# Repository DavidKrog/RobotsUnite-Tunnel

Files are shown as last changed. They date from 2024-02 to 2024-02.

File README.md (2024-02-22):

# RobotsUnite-Tunnel
Autor: <br> 
Celina Engel <br>
David Kroginski

## Hardware (Aufbau der Holzbox):
1.	**Maße der verschiedenen Bauelemente:**

Für den Bau der Holzkiste haben wir mit 10 Bauteile gerechnet, damit die Kiste stabil ist, allen Anforderungen entspricht und die erwünschten Funktionsweisen umgesetzt werden können.

Verwendet haben wir dafür:
   - 4x Seitenwände (50x65cm)
   - 2x für Deckel und Boden (50x50cm)
   - 1x zweiter Boden für den Elektronikabteil (47x47cm)
   - 2x Schiebetüre (37x37cm)
   - 1x Klappe für den Deckel (40x40cm)
<br>
<br>

2. **Maße der Ausschnitte:**

Ausschnitte haben wir an allen Seitenteilen der Holzkiste zur Stabilisierung vorgenommen (siehe Stabilisierung der Box).
   Außerdem haben wir mittig in den Deckel ein 40x40cm großes Quadrat geschnitten, um die Klapptüre für die Technikbox zu realisieren.
   Für die Schiebetüren haben wir ein 35,5x34 cm (Höhe x Breite) großes Rechteck herausgeschnitten.
   Damit die Schiebetüren auf- und zufahren können mussten an der rechten Außenwand Einschnitte vorgenommen werden. Diese wurden passgenau zum Türaufbau gewählt. 
  |  |
:-------------------------:|:-------------------------:|:-----:
<em>Ausschnitte Schiebetüre</em>| <em>Ausschnitt Deckel</em>|<em>Ausschnitte für den Auszug der Schiebetüren</em>

<br>
<br>

**Maßstab:**

Tür_Vorne |  Tür_Hinten|rechte_Seite
:-------------------------:|:-------------------------:|:-----:
<em>Türwand Vorne</em>| <em>Türwand Hinten</em>|<em>Rechte Seite</em>
Boden|Klappe_Deckel|Deckel
<em>Bodenplatte</em>| <em>Deckelplatte</em>|<em>Klappe</em>
zwischenboden|Tür|linke_Seite
<em>Zwischenplatte</em>| <em>Tür</em>|<em>Linke Seite</em>

Bei dem Zwischenboden muss man Aussparungen für Kabel und eventuell für den Endlagentaster machen. Diese sind nicht in der Skizze eingetragen, da dies je nach Montage der Elektrik in Größe und Position variiert.
<br>
<br>

3. **Stabilisierung der Box:**

Um die Holzkiste sehr stabil zu bauen haben wir uns ein simples System überlegt. Hierzu haben wir an jeder Außenkante der einzelnen Holzplatten die Hälfte der Seite um jeweils 1,5cm ausgesägt und die andere Hälfte unberührt gelassen. Somit hat sich ein recht einfaches, aber effizientes Stecksystem ergeben, welches nach der Verschraubung sich als sehr stabil und robust erwiesen hat.

  |  
:-------------------------:|:-------------------------:
<em>Ausschnitte an den Seitenwänden<em>| <em>Ausschnitte an den Seitenwänden</em>

<br>
<br>

4. **Aufteilung der Box in Arena- und Technikabteil:**

Die Holzkiste wird in einen Arena- und Technikabteil aufgeteilt.
Die Arena befindet sich in den unteren zwei Dritteln der Kiste und kann über die beiden verbauten Schiebetüren betreten und genutzt werden. Die Technik im oberen Drittel der Kiste ist einfach über den klappbaren Deckel auf der Oberseite der Box erreichbar. Im inneren der Kiste haben wir einen zweiten Boden verbaut, um die beiden Abteile abzutrennen.
Um den zweiten Boden einzubauen, werden zwei Querstreben in der Kiste verschraubt. Die Position wird von der Schiebetür und den verwendeten Auszugsschienen bestimmt. Auf diesen wird der zweite Boden angebracht.
<p>
    
   <br>
    <em>Balken zur Anbringung der Schiebetüren</em>
</p>

Bis auf die verbauten Motoren für die elektrischen Schiebetüren und die Leuchttaster für das Öffnen und Schließen dieser befinden sich alle elektrischen Bauteile in dem Technikabteil. Diese Aufteilung haben wir vorgenommen, um so gut wie alle Elektrischen Bauteile vom Rest der Box abtrennen zu können, um so mögliche Elektrounfälle zu vermeiden.
<p>
    
    <br>
    <em>Leuchtdrucktaster im Kisteninneren</em>
</p>

<br>
<br>

5. **Schiebetürmechanismus (3D-Druck und Modell der Zahnradschiene und Zahnrad):**

Die verbauten Schiebetüren wurden ein kleines bisschen Größer als der Ausschnitt an der Vorder- und Rückseite gewählt. Damit wollen wir gewährleisten, dass die Türen bündig am Gehäuse anliegen und seitlich nicht durch Schlitze hindurchgeschaut werden kann.  
Außerdem wurde am Boden eine Aussparung eingefräst, in dieser wir eine Führungsschiene verlegt haben. Somit verhindern wir, dass sich die Holztüren verhaken können.  
Damit sich die Türen leicht öffnen und schließen haben wir uns für den Verbau von Schubauszügen entschieden. Diese lassen sich sehr leicht und ohne großen Kraftaufwand bewegen.
Um die Türen elektrisch antreiben zu können wurde eine 37cm lange Zahnradschienen mit dem passenden Zahnrad 3D-Drucker gedruckt. Die Schienen werden mittig an der Schiebetürinnenseite, an den dafür vorgesehenen Laschen befestigt. Das Zahnrad wird passgenau an den Elektromotoren befestigt. Letztendlich wird der Motor in der Kiste so angebracht, dass sich das Zahnrad passend in der Zahnradschiene bewegt um die Schiebetüren auf- und zufahren lassen zu können. 
Damit die Schiebetüre problemlos aufgehen kann haben wir an der rechten Seitenwand passend Ausschnitte vorgenommen (siehe Maße der Ausschnitte). 
  |  |
:-------------------------:|:-------------------------:|:-----:
<em>Schiebetüre vorne<em>| <em>Schiebetüre hinten</em>| <em>Schiebetüre hinten ausgezogen</em>
  |  |Befestigungtür
<em>Boden der Holzkiste<em>| <em>Schiebetüren verbaut</em>| <em> Befestigung der Schiene</em>

<br>
<br>

6.	**Aufbauplan:**

<p>
    
    <br>
    <em>Aubau Holzkiste komplett</em>
</p>

<br>
<br>

7. **Verbesserungen:**
 
Während der Konstruktion haben wir gemerkt, dass nicht alles machbar ist, wie wir es geplant hatten. Dadurch mussten wir manchmal bisschen improvisieren. Dies ist einer der Gründe, warum die rechte Seite der Box die besondere Aussparung für die Schiebetür besitzt.
Damit die äußere Erscheinungsform der Box ordentlicher ist und man aus den Erfahrungen profitieren kann, haben wir für den Aufbau der Kiste teilweise die Maße noch einmal angepasst.

| ||
| --- | --- |
Boden_Verändert| Bodenplatte: <br>Aufgrund der vorher festgelegten Stabilitätsausschnitte würde eine Freifläche vor den Schiebetüren entstehen. Um diese zu vermeiden, wurden die Aussparungen an der Bodenplatte angepasst. Dies soll das Aussägen der einzelnen Teile und das spätere zusammenbauen erleichtern.|
Tür verändert| Schiebetüre: <br>Die Montage der Auszugsschiene war zu beginn des Kistenbaus anders vorgesehen gewesen. Aufgrund dessen wurden Anpassungen an der Größe der Schiebetüre vorgenommen um sich ein Zwischenbrett an der Schiebetüre für die Anbringung der Schubauszüge zu sparen.|
rechte_Seite_verändert| Rechte Wandseite: <br> Durch die veränderten Tür Maße kann man auch die Ausschnitte der rechten Außenwand anpassen. So wird das aussägen leichter und das Gesamtergebnis auch schöner.|

<br>
<br>

## Hardware (Aufbau der Elektrik):
1.	**Verwendete Bauteile und deren Funktion:**

**Siemens LOGO 8:**

Die Siemens LOGO 8 wird verwendet, um alle nötigen Programmierungen für das Projekt vorzunehmen. Realisiert wird damit der Schiebetürmechanismus, die Leuchttaster, der Single- und Multimode und die ausgedachten Rätsel. Die Programmierungen wurden mit Siemens LOGO!Soft Comfort vorgenommen.
<br>
<br>

**Netzteil (24V):**

Das 24V-Netzteil welche einen maximalen Ausgangsstrom von 4,5A hat wurde ausgewählt, da es alle verbauten Bauteile mit dem nötigen Strom versorgen kann. Ein weiterer Grund für ein 24V-Netzteil ist, dass es mit den allermeisten Bauteilen kompatibel ist. Außerdem kann bei der Gleichspannung unter 60V auf einen Schutz gegen direktes Berühren verzichtet werden. 
<br>
<br>

**Sicherungen:**

Wir nutzen Schmelzsicherungen, da diese klein und kompakt sind. Außerdem kann man diese flexibel anpassen und falls nötig nochmals zu einem späteren Zeitpunkt den abzusichernden Strom einstellen. Insgesamt werden in dem Projekt fünf Sicherungen verbaut. Jeweils eine Sicherung für die Spannungsversorgung der LOGO, für die Eingänge, welche in die Logo führen, die ersten vier Relais Ausgänge der LOGO, für die Motorsteuerung und eine Sicherung für die LEDs der Leuchtdrucktaster.
<br>
<br>

**Relais:**

In unserer Schaltung verwenden wir Relais, um die Motoren anzusteuern. Pro Drehrichtung des Motors werden 3 Relais verwendet. Ein Relais dient als Sicherung, sodass nicht durch falsches Bedienen der Motor gleichzeitig in den Rechts- und Linkslauf gelangen kann, wodurch ein Kurzschluss entstehen würde. Dies funktioniert in dem man das Relais als Öffner verwendet und in Reihe zum Spulenkontakt des zweikanaligen Relais verschaltet. Das Zweite Relais ist in Reihe zum ersten Relai und wird durch den Endlagentaster gesteuert. Dadurch kann man sicher gehen, dass der Motor aufhört, wenn die Endlage erreicht wurde.
Das dritte Relais ist 2-kanalig, wodurch es uns möglich ist, einfach und sicher zwischen den beiden Leitungen des Motors zu wechseln, um ein Richtungswechsel zu ermöglichen.
<br>
<br>

**Elektromotor:**

Für jede Schiebetüre wurde ein 12V Getriebemotor verbaut. Die Geschwindigkeit des Motors kann über die Spannungswandler und das Verwenden verschiedener Zahnradgrößen passend eingestellt werden. Die Elektromotoren werden in dem Arenaabteil verbaut, die dafür verwendeten Spannungswandler im Technikabteil. 
<br>
<br>

**Endlagentaster:**

An jeder Schiebetüre werden jeweils zwei Endlagentaster angebracht. Diese sollen einerseits den Öffnungs- und andererseits den Schließvorgang stoppen. Sobald die Schiebetüre den Endlagentaster betätigt stoppt der Motor und die Türe gerät in Stillstand. Somit soll vermieden werden, dass die Schiebetüre zu weit auffährt und aus der Führung springt, oder zu weit nach innen fährt und der Motor durch zu spätes Abschalten zerstört wird. 
<br>
<br>

**Spannungswandler:**

Die Spannungswandler werden dafür verwendet, um die 24V vom Netzteil auf die nur teilweise maximal benötigten 12V für die Leuchttaster und Elektromotoren zu wandeln. Auf den Spannungswandlern befindet sich eine digitale Anzeige, mit dieser man sehr einfach die passenden Werte einstellen kann. Die Spannungswandler werden in einer selbstentworfenen 3D-Druck Box im Technikabteil der Holzkiste verbaut. 
<br>
<br>

**Leuchtdrucktaster:**

Insgesamt wurden vier Leuchttaster verbaut, um die Schiebetüren steuern zu können. Außerhalb der Kiste wurden jeweils auf der Vorder- und Rückseite ein Taster verbaut und im inneren der Kiste genauso. Je nach Auswahl des Rätsels müssen die Leuchttaster verschieden betätigt werden, um ins Innere und dann wieder aus der Kiste herauszukommen. 
Die Leuchtaster sind dauerhaft im Leuchtbetrieb, wenn sich die Schiebtüren bewegen, dann blinken die Taster mit 2 Herz. 
<br>
<br>

2.	**Verkabelungen und Montage der Bauteile in der Technikbox (Aufbauplan):**

In der Technikbox wird die Siemens LOGO 8, das passende Erweiterungsmodul, die Relais und die Sicherungen auf einer 35mm breiten Hutschiene verbaut. 

Die Spannungswandler werden in einer 3D gedruckten Box fest verbaut. Die zwei Spannungswandler, welche für die beiden Motoren zuständig sind wurden auf 7,9V eingestellt. Der Spannungswandler für die LED-Beleuchteten Drucktaster wurde auf 10V eingestellt. 

Die sechs verbauten Klemmbausteine wurden auch auf einer Hutschiene angebracht. Die Klemmbausteine sind für die Masse der LOGO und den einzelnen Relais, den Masse für die Leuchtdrucktaster, die Spannungsversorgung der Leuchtdrucktaster, Spannungsversorgung von der LOGO zu den Relais, Ausgang aller Taster, Endlagentaster und Schaltern und für den Eingang über das Netzteil und weitergehende Leitungen um das Gesamt System zu versorgen.

Die Taster um die verschiedenen Modi und Quizes auswählen zu können wurden auch in einem 3D-Modell verbaut und anschließend in dem Technikabteil der Holzkiste verbaut und verdrahtet. 
<p>
    
   
</p>
<br>
<br>

3.	**Verkabelungen und Montage der Bauteile im Kisteninneren (Aufbauplan):**
    

5.	**Netzplan (Verkabelungsplan):**

<p>
    
</p>
<br>
<br>

## Software (Programmierungen):
1.	**Verwendung der Siemens LOGO 8:**

<p>
    
</p>
Zur Programmierung der Siemens Logo 8 verwenden wir die dazu passende Software LOGO!Soft Comfort. Mit dieser kann man ohne großartige Programmiervorkenntnisse ein Programm schreiben, welches von der Logo ausgeführt werden soll. Das Ganze wird mittels der Grafischen Benutzeroberfläche realisiert. Das Programm wird mit Logikgattern wie UND, ODER, NOR, usw. geschrieben. Man verbindet die einzelnen Gatter mit dem Pfad, um die Logik zu erstellen. Für eine bessere Übersichtlichkeit kann man die Linien auftrennen. Dabei wird am Anfang und Ende einer Verbindung ein grüner Pfeil eingefügt und die vielen unübersichtlichen Verbindungslinien entfernt. Um die Zugehörigkeiten der Pfeile nachvollziehen zu können, werden die Pfeile immer passend nach ihrem Gegenstück benannt (siehe Abbildung). So kann der Code in einzelne Netzwerke aufgeteilt werden, ohne dass es zu unübersichtlichen Verbindungsknäulen kommt. Um die Lesbarkeit des Programmcodes stark zu erhöhen, haben wir das Konzept durchgehend angewendet.
<br>
<br>

2.	**Inputs der Siemens LOGO 8:**

<p>
    
</p>
Die hier für das Projekt verwendete Siemens Logo 8 hat standartmäßig 8 Inputs zur Verfügung. 
Da wir für unser Realisiertes Projekt mehr Inputs benötigen, verwenden wir noch zusätzlich ein Erweiterungsmodul. 
In der nebenstehenden Abbildung sieht man in Gelb die von uns festgelegten und verwendeten  Inputs, welche aufsteigend nummeriert sind. 
Die Inputnummerierung stimmt mit der Nummer auf der Logo überein. Außerdem wurden die Inputs noch beschriftet, damit beim Programmieren leichter nachvollzogen werden kann, wofür der Input verwendet wird. Die Grünen Pfeile stehen für die weiteren Verwendungsorte im Programm.
<br>
<br>

3.	**Outputs der Siemens LOGO 8:**

<p>
    
   
</p>
Um die Schiebetüren steuern zu können, werden vier Outputs an der Siemens LOGO 8 benötigt. Für jeden Output ist die Steuerung sehr ähnlich aufgebaut. Es ändern sich hauptsächlich die Signale, welche verwendet werden. Zu Beginn wurden zwei Oder-Gatter verwendet, da in LOGO!Soft die Gatter nur 4 Eingänge zur Verfügung stellen. Da wir zur vollständigen Realisierung mehr als vier Eingänge benötigen, verwenden wir zwei ODER-Gatter in Reihe. Die Eingänge, welche in die Oder-Gatter gehen, kommen jeweils von vorher Programmierten Code Teilen, wo entschieden wird, dass die Tür sich bewegen soll. Weiter geht das Signal in ein RS-Glied, welches das Signal so lange hält, bis ihm gesagt wird, das es aufhören soll. Zum Stoppen wird das Signal von den verbauten Endlagentaster verwendet, womit der Zustand der Tür bestimmt werden kann. Der Ausgang des RS-Glied geht an den Output der LOGO, wo die Motorsteuerung mit Hilfe von Relais gesteuert wird. 
Mehr dazu kann im vorliegenden Verdrahtungsplan eingesehen werden. 
<br>
<br>

4.	**Programmierung des Betriebsbeginns:**

<p>
    
</p>
Diese 2 Programmausschnitte sind dafür da, die Schiebetüren der Holzkiste in die nötige Startposition zu bringen. Wenn die LOGO Strom bekommt und der Programmablauf startet, wird der Blaue Merker aktiviert. Dieser lässt beide Türen schließen, um mögliche Fehlpositionen, welche beim Transport oder dem Aufbau entstanden sein könnten zu beheben (also die Tür ist weder vollständig geschlossen noch geöffnet). In der linken Abbildung wird noch auf die Eingänge der Rätsel Auswahl geachtet. Zu Beginn sind bei jedem Rätsel beide Schiebetüren geschlossen weshalb, auf den Einschaltmoment der Inputs für die Rätselauswahl geachtet wird, um die Türen zu schließen. Die rechte Abbildung zeigt den Programmausschnitt, welcher die Türen der Kiste in die Startposition für den Single- und Team-Modus bringt. Da zu Beginn der beiden Modis die Türen zu keinem Zeitpunkt gleichzeitig geöffnet oder geschlossen sind, wird bei der Auswahl eines Rätsels die geöffnete Türe geschlossen.
<br>
<br>

5.	**Programmierungen zu Single- und Team-Modus:**

<p>
    
</p>
Verwendet man das Projekt im einfachen Single- und Team-Modus, ohne ein Rätsel auszuwählen dann wird das Parkour Element als einfacher Durchgang genutzt. 

Der hier abgebildete Code ist oben und unten symmetrisch aufgebaut.

|||
| --- | --- |
| Hier wird geprüft in welcher Stellung sind die Schiebetüren befinden.|
| Für den Singlemodus wird nur geprüft, ob einer der Taster an der Außenseite der Holzkiste gedrückt wurde.|
| Für den Teammodus wird überprüft, ob zwei Taster gleichzeitig gedrückt werden.|

Außerdem gibt es eine Abfrage, ob der Schalter für den dafür nötigen Teammodus gedrückt wurde. Die beiden Programmteile oben kommen in ein ODER-Gatter. Dieses Signal geht in ein UND-Gatter, welches den aktuellen Zustand der Türen aufnimmt, um dann die Türen anzusteuern.

|||
| --- | --- |
|Hier wird darauf geachtet, dass kein Rätsel aktiv ist. In den unteren Eingang des UND-Gatters kommen die Signale von der Grafik oben drüber. Der Ausgang steuert die Türen.|
<br>
<br>

6.	**Programmierungen zu den Rätseln:**

<p>
    
</p>
Für das Projekt haben wir uns drei verschiedene Rätselarten ausgesucht. Alle Rätsel haben den gleichen Anfang (siehe Abbildung). Dieser Programmteil ist dafür da den richtigen Programmabschnitt zu auszuwählen. Außerdem kann so verhindert werden, dass zwei Rätsel gleichzeitig ausgewählt werden können. 
<br>
<br>

Rätsel 1:

<p>
    
</p>
In der folgenden Abbildung sieht man den Programmcode für das erste auswählbare Rätsel. Das hier verwendete UND-Gatter ist dafür verantwortlich das beide Türen zu sind und die Kiste in ihrer Grundstellung steht. Dieses Signal geht in ein weiteres UND-Gatter, in diesem drauf geachtet wird, dass immer nur der richtige Schalter gedrückt wird. Daraufhin wird das RS-Glied aktiviert. Dieses wird sofort zurückgesetzt, wenn der gedrückte Taster losgelassen wird. Danach wird geschaut, ob der nächste Taster zusätzlich gedrückt wird und der Taster mindestes eine Sekunde gedrückt wird damit sich alle Türen öffnen.
<br>
<br>

Rätsel 2:

<p>
    
</p>
Im zweiten Rätsel wird gezählt, wie oft die beiden äußeren Taster gedrückt werden. Wenn beide Taster mindesten zwei-mal gedrückt wurden, geben sie das Signal weiter zum UND-Gatter, welches dann die beiden Schiebetüren öffnet. Danach werden die Zähler wieder zurückgesetzt, damit das Rätsel für den nächsten Durchgang bereit ist.
<br>
<br>

Rätsel 3:

<p>
    
</p>
Im dritten Rätsel wird mittels des oben gezeigten Programmcodes geschaut, ob die Taster in der richtigen Reihenfolge gedrückt wurden. Realisiert wird der ganze Vorgang durch ein in Reihe geschaltetes RS-Glieder. Erforderlich sind vier Tastendrücke, weshalb vier RS-Glieder benötigt werden. Bei einer falsch Eingabe werden alle RS-Glieder zurückgesetzt und die Eingabekombination muss von neuem gestartet werden. Bei richtiger Eingabe öffnen sich die Schiebetüren und das Rätsel wird wieder zurückgesetzt, damit es für den nächsten Durchgang bereit ist.
<br>
<br>

7.	**Schließen der Schiebetüren:**

<p>
    
</p>
Damit im Rätsel Modus die Türen wieder von außen geschlossen werden können ist folgender Programmausschnitt verantwortlich. Wenn irgendein Rätsel ausgewählt wurde und irgendein Taster bei offenen der Türen gedrückt wird, schließen sich alle Schiebetüren. Somit befindet das ganze Projekt wieder in Ausgangsstellung. Dies kann verwendet werden, um das Rätsel für den nächsten Durchgang vorzubereiten, oder um die Türen für den Transport zu schließen.
<br>
<br>

8.	**Schiebtüre von Kisteninneren steuern:**

<p>
    
</p>
Dieser Programmteil wird in jedem Rätsel verwendet. So wird realisiert, dass die Türen von innen immer geöffnet und geschlossen werden können. Das obere UND-Gatter öffnet die Türen, wenn sie zu sind und das untere UND-Gatter schließt sie, wenn sie offen sind.
<br>
<br>

9.	**Lampensteuerung:**

Sobald die Box eingeschaltet wird und die Bauteile Strom bekommen, leuchten die Lampen dauerhaft. Situationsbedingt blinken die Leuchtdrucktaster, um den Nutzern Rückmeldung zu bestimmten Ausführungen zu geben. 
Die Lampen sollen mit 1Hz blinken, wenn sich die Schiebtüren öffnen oder schließen. 
Wenn das Rätsel 3 in der falschen Reihenfolge ausgeführt wird und somit ein Fehler entsteht, dann blinken die Lampen für 2 Sekunden schnell mit 5Hz.
|||
| --- | --- |
| Wenn sich die Türen bewegen, dann wird auf das Signal geschaut, mit welchen die Türen gesteuert werden sollen. Solange ein Signal anliegt, gibt der Impulsgeber immer ein Blinken mit 1Hz aus. |
|Falls eine falsche Eingabe im dritten Rätsel getätigt wurde, wird das zurückgesetzte Signal auch an diesen Programmausschnitt weitergeleitet. Dieser aktiviert das RS-Glied, wodurch ein Impulsgeber mit 5Hz aktiviert wird. Dieser funktioniert solange das RS-Glied aktiv ist. Abgeschaltet wird das RS-Glied wenn die Einschaltverzögerung, welche auf 2 Sekunden eingestellt ist, aktiviert wird.|
<br>
<br>

10. **Upload Siemens LOGO:**

Um die Software auf die Siemens LOGO zu installieren, gibt es zwei Möglichkeiten. Die erste wäre mit Hilfe der Siemens LOGOSoft Comfort, welche benötigt wird, um das Programm zu erstellen. Damit kann man die geschriebene Software auf die Siemens LOGO installieren. Dieser Weg muss gegangen werden, wenn das Programm neu erstellt oder verändert wurde. Dabei ist aber eine Lizenz für das Software notwendig, welche vorab gekauft werden muss.
Hatte man das Programm schon einmal auf der Siemens LOGO installiert, kann man die Software auf der LOGO direkt auf eine SD-Karte schreiben lassen. Dies wird in der Menüführung direkt auf der Siemens LOGO erklärt wie der Download und Upload funktioniert. Dadurch kann man die Software auf eine neue LOGO installieren, ohne das ein Rechner notwendig ist. So können auch vorhandene LOGO Programme geladen werden ohne eine Lizenz zu besitzen. Über diesen Weg sind aber keine Veränderungen am Programm möglich!

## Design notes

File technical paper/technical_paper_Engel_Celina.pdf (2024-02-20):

Engel,Celina / 29.12.20 ©2023 IEEE

# Planning and construction of an automated parkour element with sliding-door mechnaism for the Robots unite event

Celina Engel
Nuernberg Institute of Technology -Georg Simon Ohm
Nuernberg, Germany
[engelce87373@th-nuernberg.de]

Abstract—This technical paper presents the process and construction of an automated parkour element. In the course of the project, mechanical, electrical and programming aspects are dealt with. At the beginning, all components are analyzed and presented individually with regard to their functions and project integration. One of the main goals of the documentation is to present the findings and work steps of the project in such a way that they can be transferred to similar project types.

I. INTRODUCTION
n 2023, the use of robots in all kinds of work areas increased significantly. In addition to their use in manufacturing processes, they are also more often being integrated into elderly care and restaurants. Due to the ever-increasing importance of robotics in everyday life, there is now an ever-increasing number of robotic courses in schools. This should make is easier for interested young people to get into programming in a playful way and offer them the opportunity to learn certain subject areas at an early stage. In order to be able to put the skills they have learned to their own robots on a wide variety of parkour elements for previous skills and possible weak points. As there was no automated parkour element yet, my fellow student and I decided to built one and make it available for the events.

II. PLANNING AND COMPONENTS
The automated parkour element consists of various mechanical, electrical and static components. The interaction of the individual components ultimately determines how well and smoothly the automated sliding door process works after a groper is being pressed by a robot. In order to be able to open and close the two installed sliding doors automatically, PLC programming is used, which is implemented using gate logic.
The element is divided into the arena area in which the robots move and the technical area in which all components necessary for the realization of the project were installed.
A. Specification of the project
The project had a few specifications that had to be observed. The passage elements must have a tube diameter of 50cm. Accordingly, the robots may only be large enough to fit through the sliding doors and overcome the parkour element. Furthermore, all electrical components should not be accessible from the outside. It is important, that these are installed inside the box to avoid possible electrical accidents. In addition, the element should be designed and automated in such a way that it can be overcome by a single robot as well as by two in a team. To make the overcoming process more difficult for the team, three puzzles were programmed. All options can be selected in advance in the technical compartment using switches. The most important specification was the structure and robustness of the wooden box.

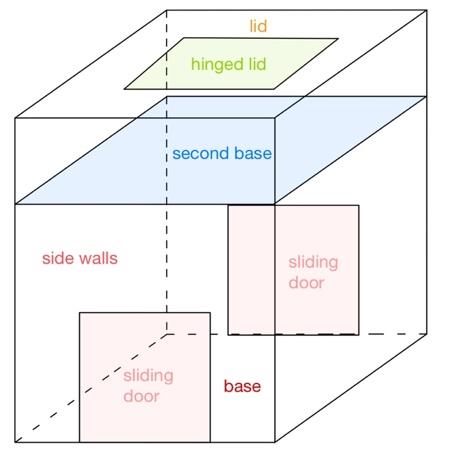
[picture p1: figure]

Figure 1:Structure of the parkour element

B. Mechnanical and static components
The robustness of the wooden construction, which is a wooden box with two sliding doors and two separate compartments, was particularly important for the project. As the wooden box is to be used more frequently and regularly in competitions and for training purposes in the coming years, it must be built to be very stable. The box must be able to withstand vibrations from robots when they drive against it. For this reason, the decision was made to use 15mm thick USB plates, which were screwed together using an interlocking system. In addition to the external construction, stable sliding drawers were also required for the sliding doors. The sliding door run in a track laid in the floor to prevent them from interlocking. As this is an automated sliding door mechanism, gear rack with a matching gear wheel had to be fitted on both sides. In addition, a construction was needed for the inner buttons to ensure that they are stable. Ultimately, the weight of the construction was a problem, which is why handles were mounted on both sides.

I

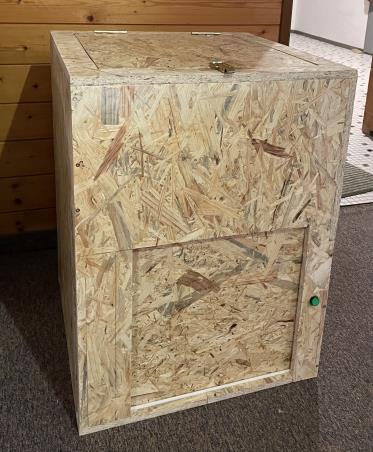
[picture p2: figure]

Figure 2: Wooden Box Construction

C. Electrical components
The electrical components are essential to automate the parkour element. Motors are installed on the sliding doors which open or close after a push of the installed buttons. The driving process is stopped at the respective installed limit switches. In order to systematically safeguard all the components, fuses were installed which trigger in the event of a fault and safeguard the remaining components. All installed elements were considered for the correct selection of fuses. The sliding door mechanism was not only protected on the software side but also on the hardware side by means of relays. The relays were installed for each running direction of each motor. This to prevent both left- and right-hand operation being controlled at the same time. To ensure that only the maximum required voltage is applied to the respective components, voltage transformers had to be installed for the motors and illuminated pushbuttons. The voltage transformer can also be used to adjust the speed of the sliding doors.

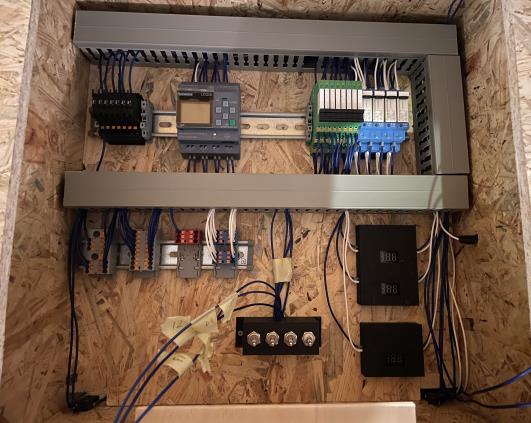
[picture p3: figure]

Figure 3:Electrical Components

D. Programming
All planned automations were implemented by using PLC programming. A Siemens LOGO 8 and a suitable expansion module were used to implement all functions. As the LOGO is small and compact, it is actually perfect for out project because the space in our technical compartment is relatively limited. It is also a good alternative to a large PLC as it is in the lower price segment. The PLC and the module each have inputs and relay outputs that are easy to connect. The simple gate logic, which we used for most programming, is very easy to understand and therefore no extensive programming knowledge is required to advance. Advantageous of the
LOGO-Soft | software, | which | is | required | for
programming, is that all programmed functions can be tested and simulated immediately.

III. DOKUMENTATION
The documentation is a very important part of the entire project. With the help of this, it should be possible for every reader to understand, rebuild and implement the project. The documentation should therefore be very structured and not too complicated. The many pictures and CAD-models make it easier to rebuild the automated parkour element.
A. Event participants
The replica is particularly important for participants of the robots unite event. With the help of the documentation, every step of the procedure can be reproduced and copied. In this way, equal opportunities can be created at the event, because every participant is able to rebuild the automated element and then use it for the necessary training purpose. In this way, the students can test their self-built robots on the element and implement or optimize any necessary functions.
B. Finding location
In GitHub the documentation can be viewed and read by anyone interested. All process steps, implementation and component dimensions can be found in the large documentation on Git. There is also a smaller documentation, which can be found in the lid of the technical compartment. With the assistance of this it is much more easier to understand how to select the puzzles correctly.

IV. CONCLUSION
Although the automated parkour element is not the biggest and most demanding project, but it is still very costly and time-consuming to plan and build. We were able to make good use of what we had learned during our studies to fully realize and complete the project. The documentation allows us to avoid mistakes, which also saves a few costs and time. We would therefore be delight if our parkour element is well received at the event and soon becomes an integral part of it.
V. ACKNOWLEDGEMENT
Last but not least ´, many thanks to Prof. May, who gave us the chance to carry out this project without any big major restrictions. I am happy to be a small part of the “Robots unite” event due to the construction element. Many thanks to David Koginski for the good and smooth cooperation, which helped to complete the project very quickly.

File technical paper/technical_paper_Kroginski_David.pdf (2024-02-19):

# Interactive parkourelement for “Robots Unite”

David Kroginski
Nuernberg Institute of Technology -Georg Simon Ohm
Nuremberg, Germany
kroginskida87346@th-nuernberg.de

Abstract—This technical paper shows the work, which has been done by two students of electrical engineering during a student project, supervised by one professor. This will be about the process from planning to construction, the problems faced during the project and how an enrichment for “Robots Unite” is build.

Keywords—robots, tournament

I. INTRODUCTION
It exists a mayor number of tournaments, where teams are building complex robots and then competing against each other. For a student it is often very difficult to get started, even if they are very interested in robotics. The problems are that often the robots get very expensive, even by building and programming it by themselves. Also, it is hard to start, if they are new and do not get help, especially during the beginning phase. For that reason, our professor started the tournament “Robots Unite”. In this tournament students from schools are making a team and building their own robots. Because of the regulations, the robots are smaller and cheaper, this is why this tournament is more affordable. Also, our University, the TH Nuremberg, is in contact with the participating school in the region. That is a big advantage for the students, because there are in contact with a university and the professors, what can be helpful for developing their own robots. With that everything the hurdle to start robotic is much smaller and the students have a great opportunity to enhance their skills. At the moment, the robots are fighting, by getting through a static parkour as fast as possible. The wish of the organizer is, that the robots have to work together, so even during the development of the robots communication between the team is needed. For that we want to develop an interactive parkour element, that one robot alone cannot get through alone. With some interactive parkour elements, the tournament can get more exciting and versatile. For the parkour elements, it must be built in a way, that the students can easily rebuilt it by themselves, improve it and add more features.

II. PROJECT DESCRIPTION
The project is an addition for the tournament “Robots Unite”. Therefor we wanted, that our parkour element is fitting to the rest of the parkour and tournament. We visited the finals in Nuremberg to get a feeling for the spirit of the tournament. The students are working in their teams together to be sure that everything is working. They are making adjustments to the robots, so it fits better the parkour, which is set up for the day. Testing the software, so they can control the robot wirelessly and make sure it is dependable. Every team has their supervisor helping them with his knowledge and experience. The communication between the different teams was hold at a minimum because they are competing against each other. The organizer wants to change it. Changing the tournament, a bit, so at least two teams have to work together, to be able to finish the whole parkour in the given time limit. We watch the finals and get some ideas for our interactive parkour element, which we started planning for afterwards. Everything will be well documented, so it is easy to rebuild, and very easy to operate, so at the tournament everyone can set it up. For our project we had four main phases. Getting ideas and planning everything, building the construction, programming, and documentation.

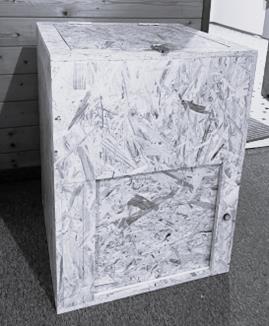
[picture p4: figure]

Figure 1 Finished parkour element

A. Idea and planing
At the beginning of the project, we were collecting ideas. The base idea of the tournament is to build a rescue robot, which can get to hard to reach places and make something. So, the main function of our parkour element will be a box with two sliding doors on the opposite sides, which are electrically powered by an electric dc motor. The robots will have to do something to be able to open it. Next to the doors will be push button, which has to be used by the robots in order to open the door. We wanted to make it more versatile, consequently we thought of more than one mode. The box is getting a single and a team mode, but also three puzzles. For the difficulty we planned multiple stages. The First stage is, what we are building, with the push buttons for the robots to operate. A possible next stage could be a circuit braker or a ball valve to operate, to make the situation a bit more realistic. This can be done by the next group working on this project, but before this, the first stage has to be tested on the next event. Afterwards we planned the whole construction of the parkour element. The next planning phase was about the electrical hardware and what are we using to control everything. There were two possibilities, a microcontroller, or a plc. We decided for the plc because it is more robust and is more reliable. This was for us particularly important, so that the parkour won’t cause any trouble during the tournament. Also plans for the wiring were made, with details like relays and fuses. The last step in the planning phase was, how are we making the hardware stuff safe, that if the plc is programmed wrong, or an error occurs, nothing gets destroyed. For that we designed a relay logic, which prevents a short circuit by wrong operation of the electric motors. Not only we thought about the hardware safety, but also about the safety for the builder and operator.

We tried to make it as safe as possible, especially about what happens if something or someone is in the door movement.

B. Construction
We had a maximum space given, in which we had to realize everything, the mechanic and the hardware. We thought about, how to build it in a way that it will be easy to rebuild. In this phase we learned how quickly the plans can change, because what we thought was not possible to realize. We build it with 15mm OSB wood to make it strong enough, so nothing happens if the robot is driving against it. This material is also rather simple to process. For greater stability and easier assembly, we made a plug system. We have a two-layer design. A lower layer for the robot to operate and a second layer on top of the first layer for the human to operate
and | where | the | electrical | hardware | is | placed.

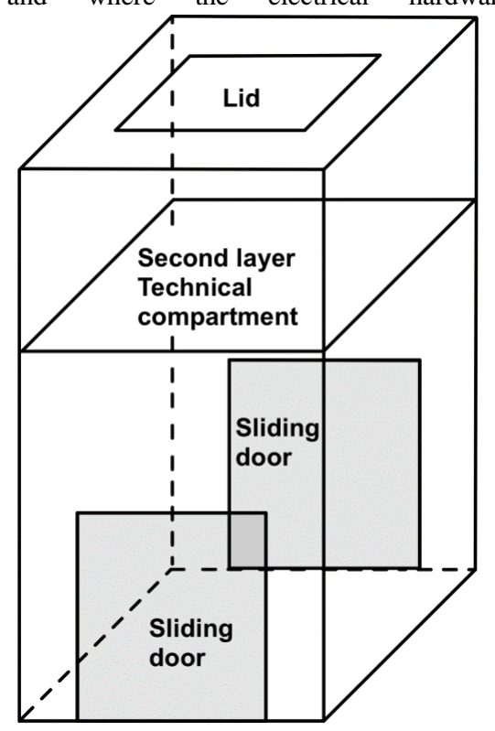
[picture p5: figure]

Figure 2 Sketch of the layout for construction

C. Programming
All functions need to be programmed. Because we use a plc, we must use their software. We use a Siemens LOGO as our plc, so we used “Siemens LOGO! Soft Comfort”. In this program the functions are programmed in a graphical way with logic gates. In this way no prior programming knowledge is needed. Simple functions are very easy to implement. If a function is complex, it needs a bit of logical understanding to realize it. An advantage of the program is, that the functions can be simulated and tested. In our stage the program covers five different functions, which can be used for training or in the tournament. By our program, which will be well documented we want to give a good base for future improvements by the students or the next team.
D. Documentation
For us it is not only important that our parkour element is working, but also that it can be used by everyone in the community. For that, a very good documentation is important. We want to make an article on GitHub, where everything can be found. There will be the plans for the wooden construction for the box, the hardware used and how to wire everything up, and the program. An advantage of the plc is, that if the program is available, it can be loaded on a micro-SD card and the plc flashes from it. With that everything the first startup can be done by everyone. With all the documentation the next group can adapt their ideas for a stage two. By making it public, everyone of the community can help and share their ideas for new functions. Also, we will give advises how to plan everything when it will be rebuilt. The documentation will be hold at the most current state. In the elements itself, the technical compartment will be labeled in a way, so for putting it in operation no extra directions will be needed.

III. CONCLUSION
The project is not one of the demanding from the technical site, but it still was challenging to complete. We learned how to start a project and plan everything, even when the plans have to be revised during the process of construction and programming. We will be happy when we will see it in use in the next event of “Robots Unite”. We gave our best, but we found details that can be done better at the next version, which will be updated in the documentation. Hopefully, our work will be valued by the community and maybe we will see our parkour element be used somewhere over the world.

IV. ACKNOWLEDGMENT
I want to thank Prof. Stefan May for giving us the opportunity to make a part for “Robots Unite”, where we got to know how much work and effort in planning it takes for even small projects. I am also thankful for the thrust given to us and the freedom, so we could decide a lot of the details and realizing our own ideas and the help during that process. Also, I am thanking my partner for that project Celina Engel, for the good and reliable work during the project. Also, I am thankful, that we could use her place as a workplace during the project.

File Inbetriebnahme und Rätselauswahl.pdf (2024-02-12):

1. Netzteil in die Steckdose und die Buchse an der Außenseite der Kiste stecken um das System mit Strom zu versorgen
2. Rastschalter 1 auswählen -> Single- oder Teammodus
3. Rastschalter 2-4 -> Auswahl der Rätsel (ACHTUNG! Nicht jedes Rätsel alleine lösbar)

Singlemodus:

Die Laufrichtung der Schiebtüren ist immer entgegengesetzt. Nach Knopfdruck, egal ob innerhalb oder außerhalb der Kiste bewegt sich die eine Türe auf und die andere zu. -> Gedacht als Druchgangspassage

Teammodus:

Die Türen arbeiten entgegensetzt wie im Single-Modus. Die einzige Änderung ist das zwei Taster immer gleichzeitig gedrückt werden müssen. Die Tastenkombination ist egal (außen/außen, innen/innen, außen/innen).

Rätsel 1: (Ausgangssituation: Kiste ist von beiden Seiten erreichbar und beide Türen sind verschlossen. Ein QR-Code mit einem zu erreichenden Punkt ist im inneren und ein QR-Code mit der Anleitung zum Türöffnen ist außen befestigt) -> Nur im Team möglich

Im QR-Code steht, dass zuerst der Taster der vorderen Tür gedrückt und gehalten werden soll. Dann soll der Taster der hinteren Tür gedrückt gehalten werden. Nach einer Sekunde soll sich die Türe öffnen und ein Roboter kann in das innere der Kiste fahren. Im inneren der Kiste muss einer der beiden Knöpfe gedrückt werden, damit sich die Türen schließen um den QR-Code auf der Innenseite der Schiebetür zu scannen. Nach dem scannen kann einer der inneren Taster gedrückt werden und die Türen öffnen sich wieder. (Drücken der inneren Taster schließt und öffnet die Türen). Um die Türen zu schließen reicht immer irgendein Taster aus.

Rätsel 2: (Ausgangssituation: Kiste ist von beiden Seiten erreichbar und beide Türen sind verschlossen. Ein QR-Code mit dem zu erreichenden Punkt ist im inneren und ein QR-Code mit der Anleitung das Element zu überwinden außen) -> Im Team oder als Single möglich

Im QR-Code steht, dass beide Taster außen 2-mal gedrückt werden müssen. Die Reihenfolge spielt dabei keine Rolle, Hauptsache beide Taster werden jeweils 2-mal gedrückt. Nachdem sich die Türen geöffnet haben fährt ein Roboter in die Kiste und muss einen der beiden inneren Taster drücken, damit sich die Türen schließen um den QR-Code auf der Innenseite der Schiebetüre zu scannen. Durch kurzes drücken der Taster auf der Innenseite öffnen oder schließen sich die beiden Schiebetüren. Um die Türen zu schließen reicht immer irgendein Taster aus.

Rätsel 3: (Ausgangssituation: Kiste ist von beiden Seiten erreichbar und beide Türen sind verschlossen. Ein QR-Code mit einem zu erreichenden Punkt ist im inneren und ein QR-Code mit der Anleitung zum Türöffnen ist außen befestigt.) -> Im Team oder als Single möglich

Im QR-Code steht, dass beide Taster außen 2-mal gedrückt werden müssen. Die Reihenfolge spielt dabei Roll. Die Reihenfolge muss mit dem hinteren Taster begonnen werden und dann müssen die Taster abwechselnd gedrückt werden. Bei falscher Eingabe blinken die Lampen schnell und die Eingabe zum öffnen muss von vorne eingegeben werden. Nach dem öffnen der Schiebetüre fährt ein Roboter in die Kiste und muss einen der beiden inneren Taster drücke um die Türen wieder zu schließen um den QR-Code auf der Innenseite der Schiebetüre zu scannen. Durch kurzes drücken der inneren beiden Taster schließt und öffnet sich die Schiebetüre.

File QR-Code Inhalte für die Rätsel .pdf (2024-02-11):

QR-Code Rätsel 1:

- Roboter 1 muss Taster 2 gedrückt halten
- Roboter 2 muss Taster 1 gedrückt halten
- Öffnen der Türen um QR-Code im inneren scannen zu können
- Taster im inneren drücken um Schiebetüren öffnen oder schließen zu können

QR-Code Rätsel 2:

- Roboter muss Taster 1 und Taster 2 zwei mal nacheinander drücken
- Reihenfolge des Drückvorgangs ist egal
- Öffnen der Türen um QR-Code im inneren scannen zu können
- Taster im inneren drücken um Schiebtüren öffnen oder schließen zu können

QR-Code Rätsel 3:

- Beide Taster müssen abwechselnd jeweils zwei mal gedrückt werden
- (z.B. Taster 1, Taster 2, Taster 1, Taster 2)
- Öffnen der Türen um QR-Code im inneren scannen zu können
- Taster im inneren drücke um die Schiebetüren öffnen oder schließen zu können

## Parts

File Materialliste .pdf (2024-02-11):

### Materialliste

- 4x Seitenwand (50x65cm)
- 1x Deckel (50x50cm)
- 1x Boden (50x50cm)
- 1x zweiter Boden für den Technikabteil (47x47cm)
- 2x Schiebetüre (37x37cm)
- 1x Klappdeckel (40x40cm)
- 2x Querbalken (47 cm) (zum Anbringen der Schiebetüren und Abtrennung Technikabteil)
- 2x kleines dünnes Holzbrett (21x3,5 cm) (für die Anbringung des Tasters im Kisteninneren (vorne))
- 2x kleines dünnes Holzbrett (21x6 cm) (für die Anbringung des Tasters im Kisteninneren (seitlich))
- 2x Holzbrett (37x7cm) (Anbringung der Schiebtüre an dem Querbalken)
- 2x Scharnier für den Klappdeckel
- 8x kleine Winkel für die Konstruktion der inneren Taster
- 2x Zahnstange (37cm)
- 2x Zahnrad (passend zur Zahnstange)
- 2x Schubauszug (Kugelvollauszug für Schubkästenlängen von 350mm)
- Hutschiene (1 mal 40x3,5cm, 1 mal 20x3,5cm)
- Führungsschiene Plastik (48,5 cm Länge, 2 cm Breite, 1 cm Höhe)
- Kabelkanal (1mal 15cm, 2mal 47cm)
- Schrauben (Lang + Kurz)
- Schrauben mit Gewinde + Muttern (für Verschraubung der Winkel mit den dünnen Holzbrettchen (Taster Halterung innen))
- 2x Klappgriffe (zum Tragen der Kiste)
- 1x Siemens LOGO 8
- 1x Siemens LOGO Erweiterungsmodul
- 4x Kippschalter mit 3 Stellungen
- 3x Spannungswandler (Motoren und LEDs)
- 1x Netzteil
- 1x Netzteilbuchse (Anbringung so das man es von außen anstecken kann
- 6x Sicherungen
- 8x Relais
- 4x Relais (Koppelrelais mit zwei Wechslern)
- 5x 6er Klemmblock
- 1x 18er Klemmblock
- 4x Endlagentaster (Für die Schiebtüren)
- 2x Motor (für die Schiebetüren)

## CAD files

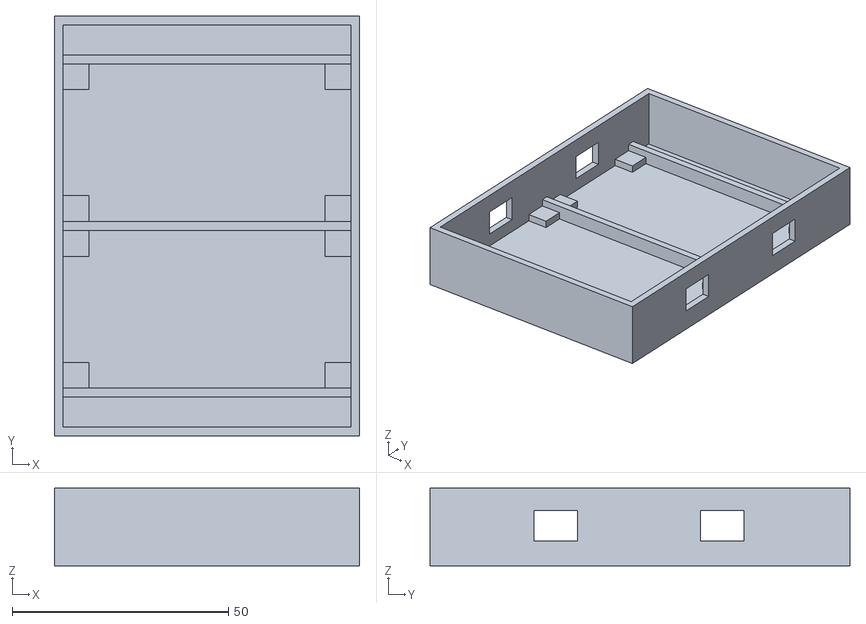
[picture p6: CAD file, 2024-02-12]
3D druck Modelle/spannungswandler_gross_box.stl
70.5 x 97.0 x 18.0

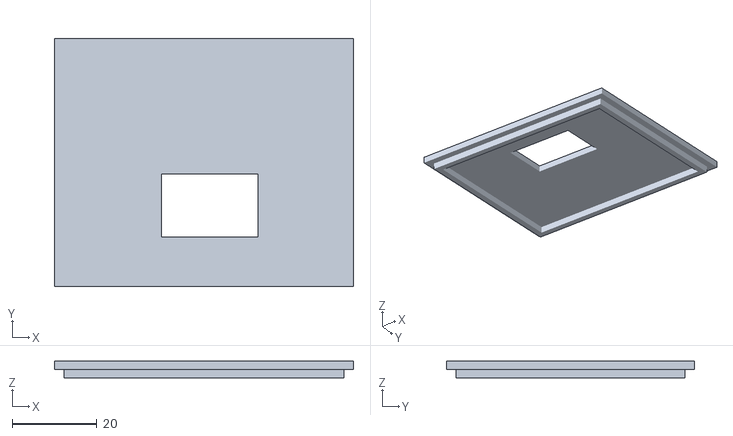
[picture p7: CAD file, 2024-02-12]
3D druck Modelle/spannungswandler_deckel.stl
70.5 x 58.5 x 4.00

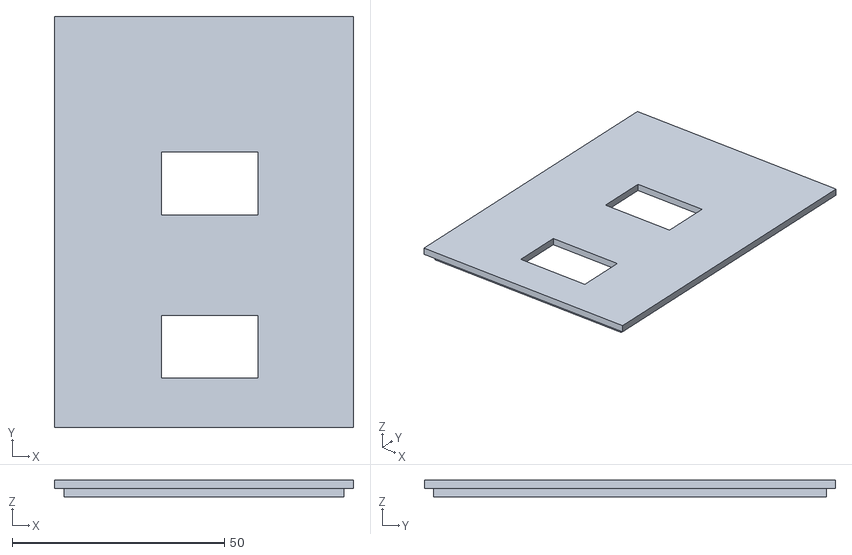
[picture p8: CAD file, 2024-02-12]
3D druck Modelle/spannungswandler_gross_deckel.stl
70.5 x 97.0 x 4.00

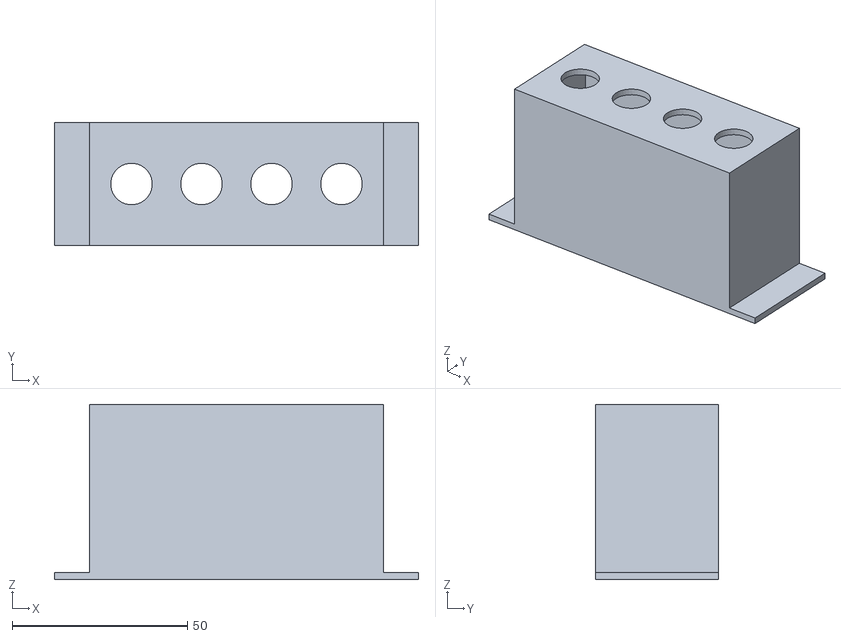
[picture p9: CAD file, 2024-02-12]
3D druck Modelle/halter_kippschalter_neu.stl
104.0 x 35.0 x 50.0

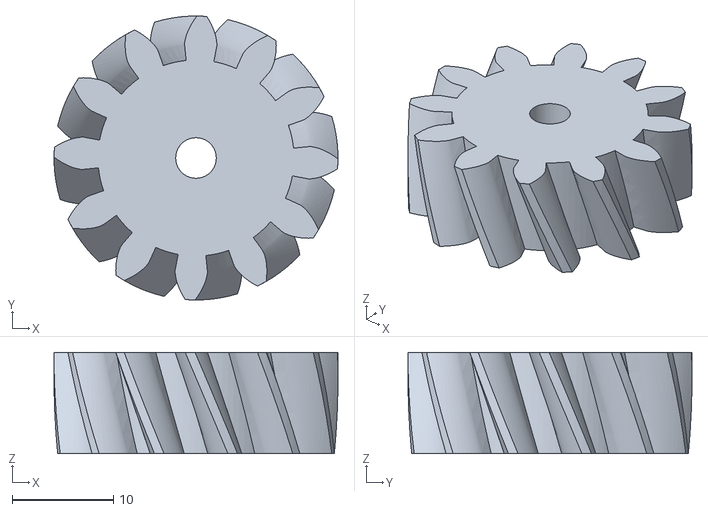
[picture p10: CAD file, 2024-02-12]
3D druck Modelle/Zahnrad.stl
28.0 x 28.0 x 10.0

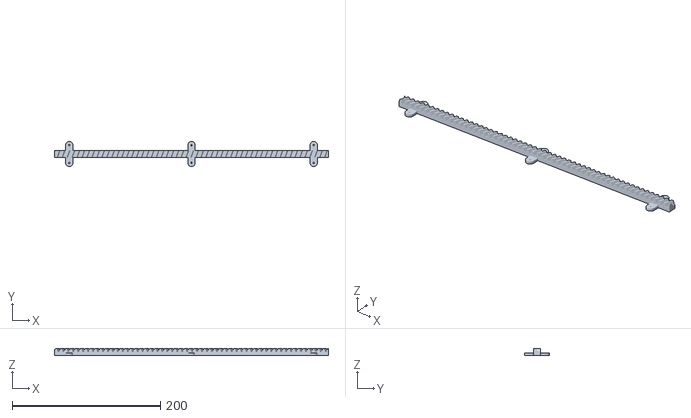
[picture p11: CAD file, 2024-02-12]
3D druck Modelle/Zahnstange.stl
370.0 x 33.9 x 9.00

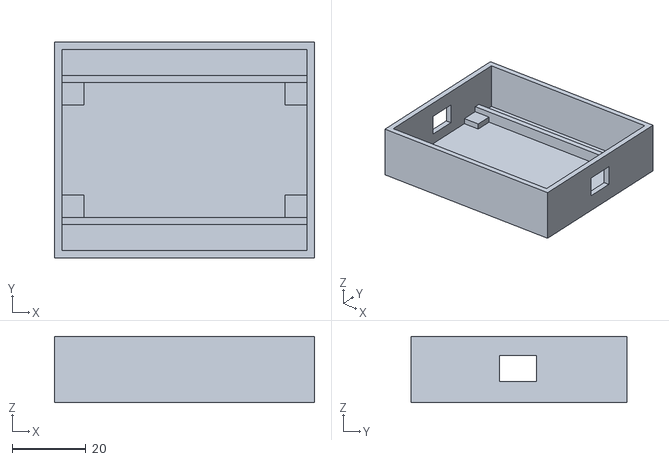
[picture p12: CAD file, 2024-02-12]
3D druck Modelle/spannungswandler_box.stl
70.5 x 58.5 x 18.0
